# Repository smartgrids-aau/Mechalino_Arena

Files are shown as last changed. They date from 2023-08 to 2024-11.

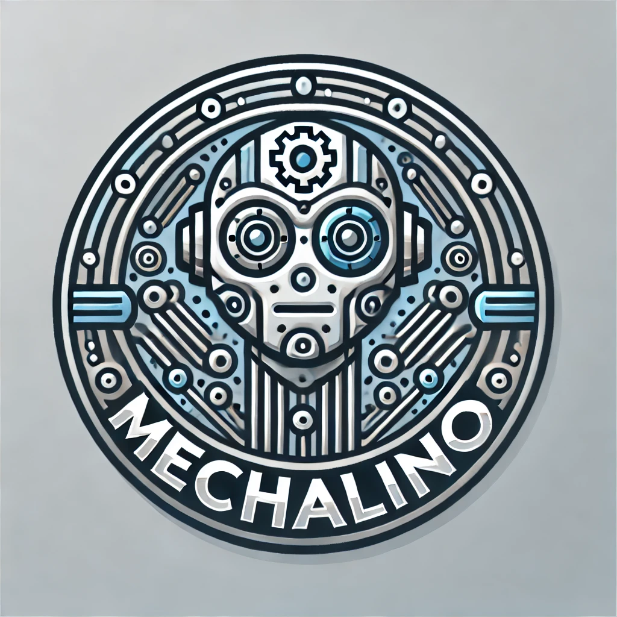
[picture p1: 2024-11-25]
mechalino_robot/hardware/PCB design/layer_2/Redesigned/Images/DALL·E 2024-07-06 23.29.42.webp

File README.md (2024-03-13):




# Mechalino Arena

## Final goal:
Implement the SCPP algorithm to Mechalino robots
## Planned steps::
 - [X] **Step 1.0** - Visualize single layer Mechalino robots in Unity 3D with a ROS backend
 - [ ] **Step 2.0** - Re-implement the SCPP algorithm in ROS
 - [ ] **Step 2.1** - Run the SCPP algorithm in ROS while robots are doing the same movements
 - [ ] **Step 3.0** - Visualize two-layer Mechalino (with sensors) in Unity 3D with a ROS backend
 - [ ] **Step 3.1** - Run the SCPP algorithm in ROS while robots are doing the movements and also delivering sensor data (obstacle detection)
 - [ ] **Step 3.2** - Use two-layer Mechalino robots to run the SCPP algorithm independently and Visualize the result in Unity 3D with a ROS backend
  _____________________________________________________
  
  **[Temporary note]** This is just a raw list and will change. 
_____________________________________________________

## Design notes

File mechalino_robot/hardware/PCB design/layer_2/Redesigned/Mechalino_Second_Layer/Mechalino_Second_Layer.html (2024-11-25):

Reporting Options

# File in Newer Format

Date | : | 30/10/2024
Time | : | 11:04:13
Filename | : | C:\Users\lukak\OneDrive\Dokumente\AAU\Bachelorarbeit\Mechalino_Arena\mechalino_robot\hardware\PCB design\layer_2\Redesigned\Mechalino_Second_Layer\Mechalino_Second_Layer.PrjPcb

Version | Warning

Release 23.10

CAUTION - This project contains rules defined using the Constraint Manager. You are seeing this message for two possible reasons. Firstly, this is an older version of the software that does not support this feature, in which case design rules will fall back to being presented as standard, query-based rules. If you save the PCB project in this older version of Altium Designer, all Constraint Manager data structure information will be lost. Secondly, if this software version does support the feature, then you currently don't have the level of Altium Designer Software Subscription (Pro/Enterprise) to be able to edit constraints using the Constraint Manager, in which case it will present rules in view only mode.

This file was generated by a later version of the software

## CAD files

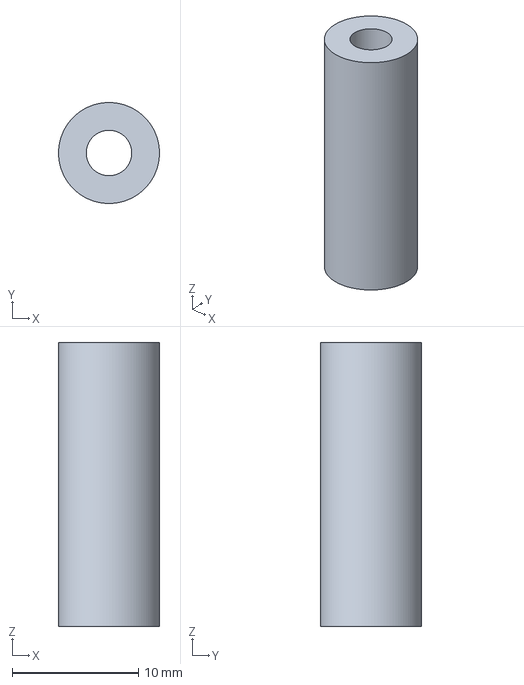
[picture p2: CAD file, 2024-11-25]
mechalino_robot/hardware/3D_designs/layer2.3mf
8.00 x 8.00 x 22.5 mm

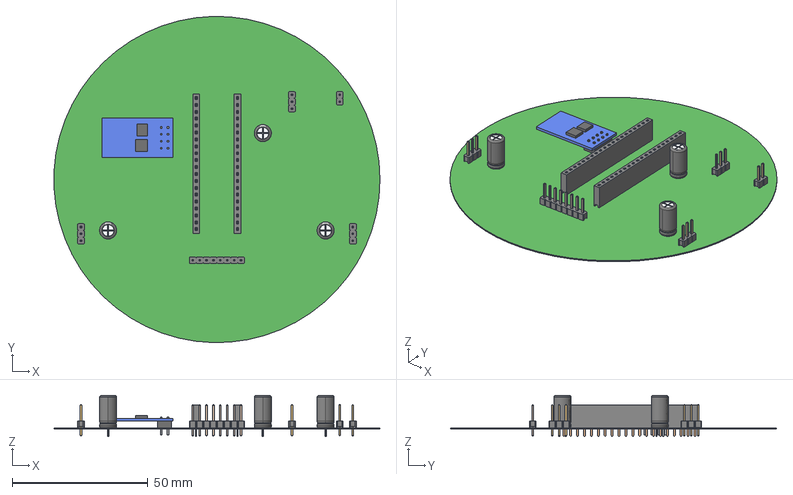
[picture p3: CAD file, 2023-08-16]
mechalino_robot/hardware/PCB design/layer_1/FAB-SwarmlyExplorerBot-A.6/ExportSTEP/PCB.step
119.9 x 120.0 x 15.2 mm
6130xx11121_PIN x 8
6130xx11821_PIN x 40
Extruded x 12
User_Library-Cap-EL(6_3x12-2_5) x 3

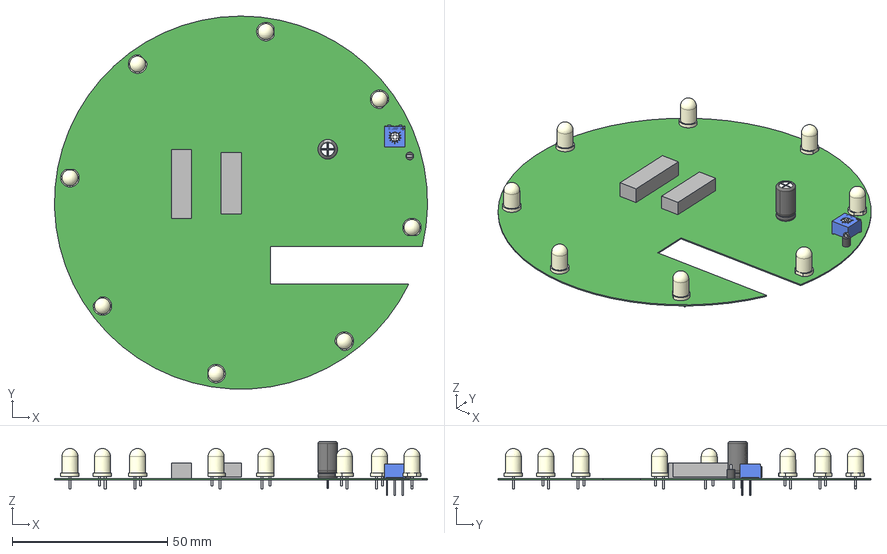
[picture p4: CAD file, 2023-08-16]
mechalino_robot/hardware/PCB design/layer_2/FAB-SwarmlyExplorerBot_layer2-A.8/ExportSTEP/PCB.step
120.0 x 119.9 x 17.5 mm
User_Library-Cap-EL(6_3x12-2_5)
User_Library-Bourns_3362P
Extruded x 2
SNR2-2.54-D5.0MM x 8

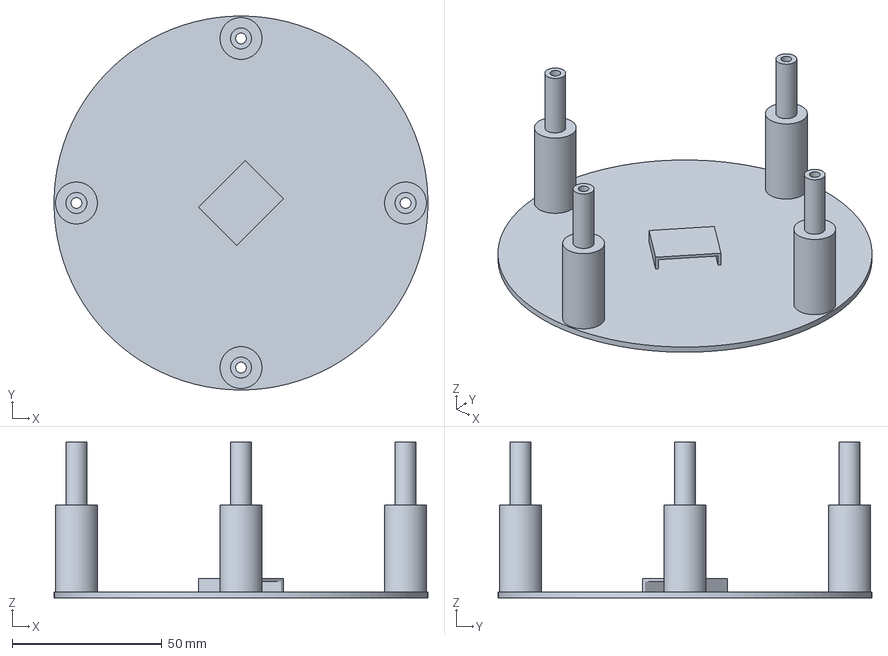
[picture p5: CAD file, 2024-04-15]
mechalino_robot/hardware/3D_designs/Head.3mf
125.0 x 125.0 x 52.0 mm

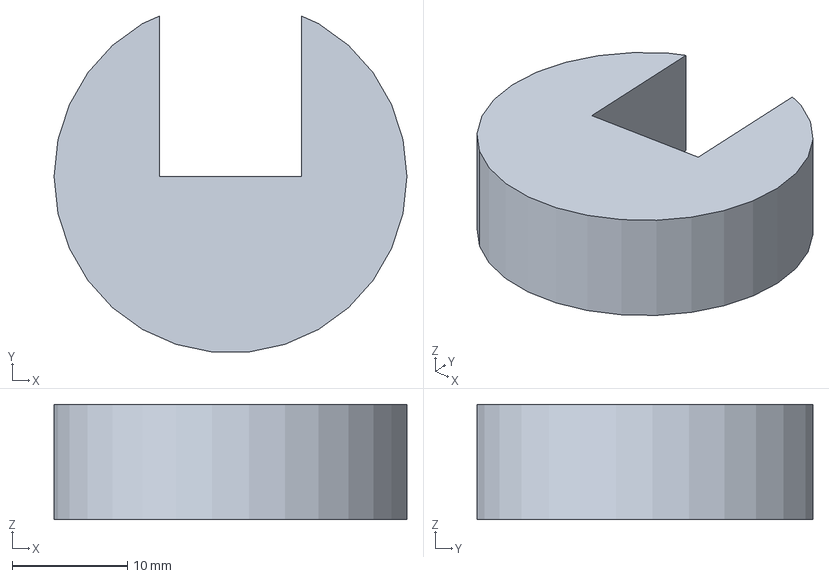
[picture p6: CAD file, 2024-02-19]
mechalino_robot/hardware/3D_designs/obstacle_holder.3mf
30.6 x 29.1 x 10.0 mm

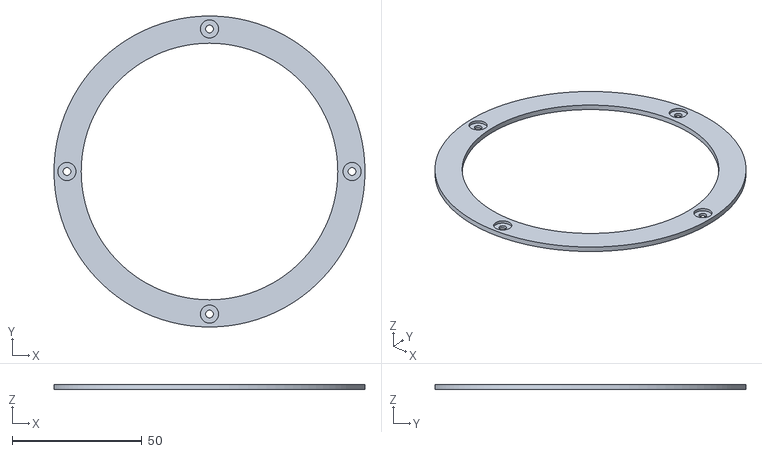
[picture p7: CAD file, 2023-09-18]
mechalino_robot/hardware/3D_designs/Head_p1.stl
120.0 x 120.0 x 2.00

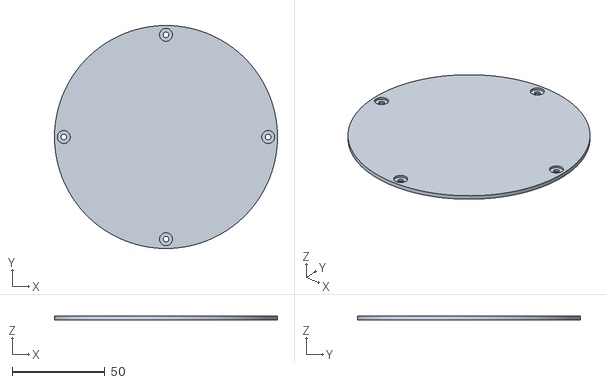
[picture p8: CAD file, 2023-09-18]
mechalino_robot/hardware/3D_designs/Head_p2.stl
120.0 x 120.0 x 2.00

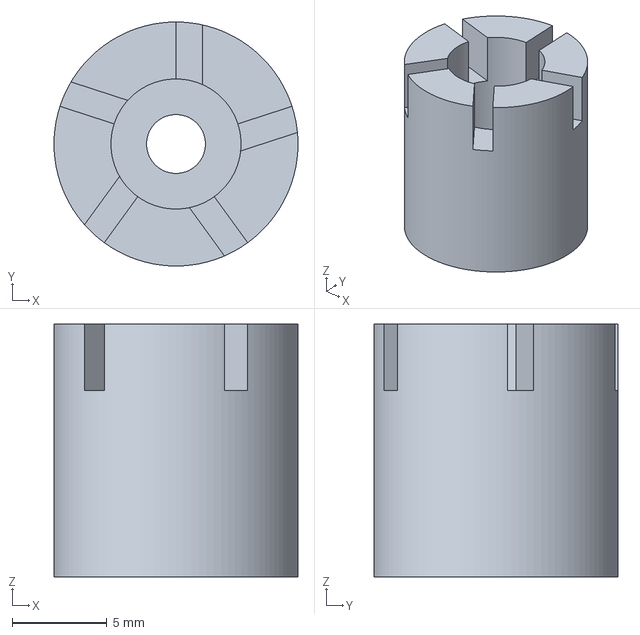
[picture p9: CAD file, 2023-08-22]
mechalino_robot/hardware/3D_designs/wheels1.3mf
12.8 x 12.8 x 13.3 mm

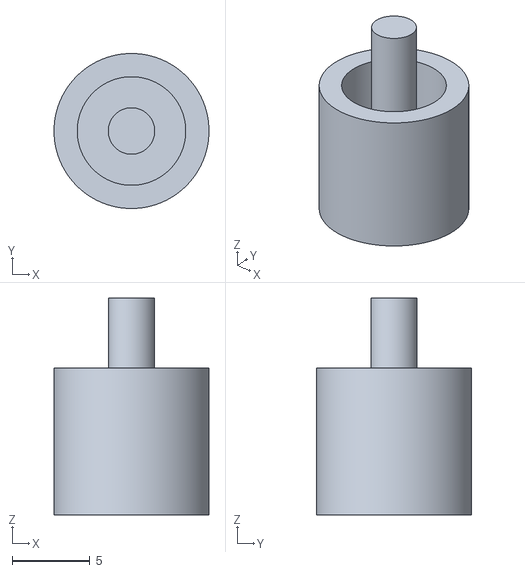
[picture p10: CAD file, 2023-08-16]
mechalino_robot/hardware/3D_designs/wheels5.stl
10.0 x 10.0 x 14.0

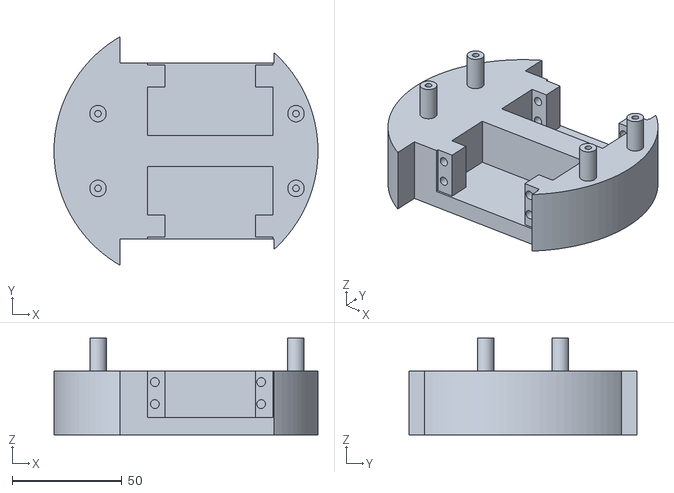
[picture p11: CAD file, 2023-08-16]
mechalino_robot/hardware/3D_designs/body.stl
120.0 x 103.9 x 44.0

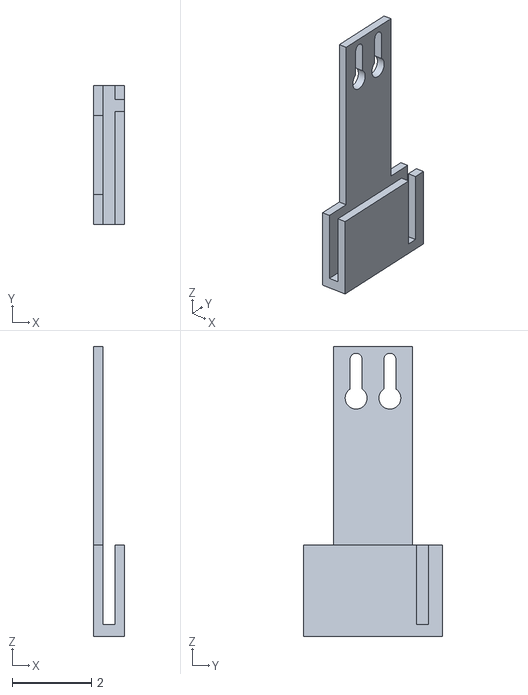
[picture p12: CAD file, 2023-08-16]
mechalino_robot/hardware/3D_designs/camera_holder.stl
0.79 x 3.50 x 7.30

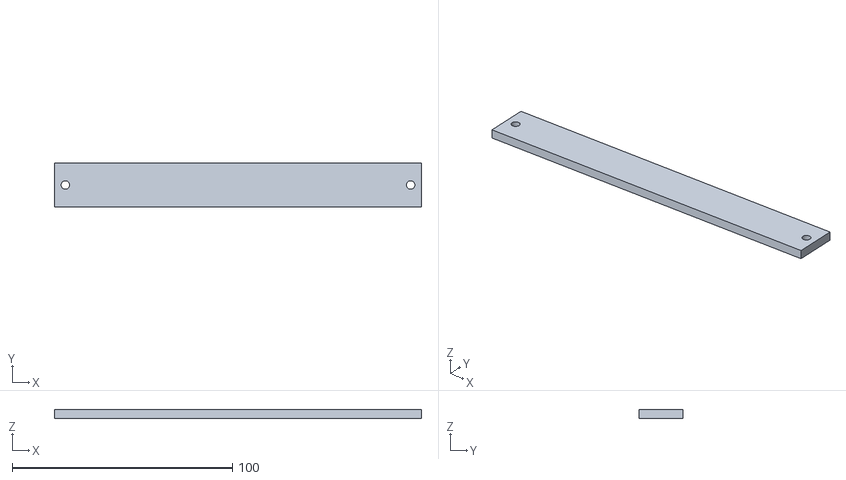
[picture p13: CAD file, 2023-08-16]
mechalino_robot/hardware/3D_designs/camera_holder_V2_Top.stl
166.7 x 20.0 x 4.00

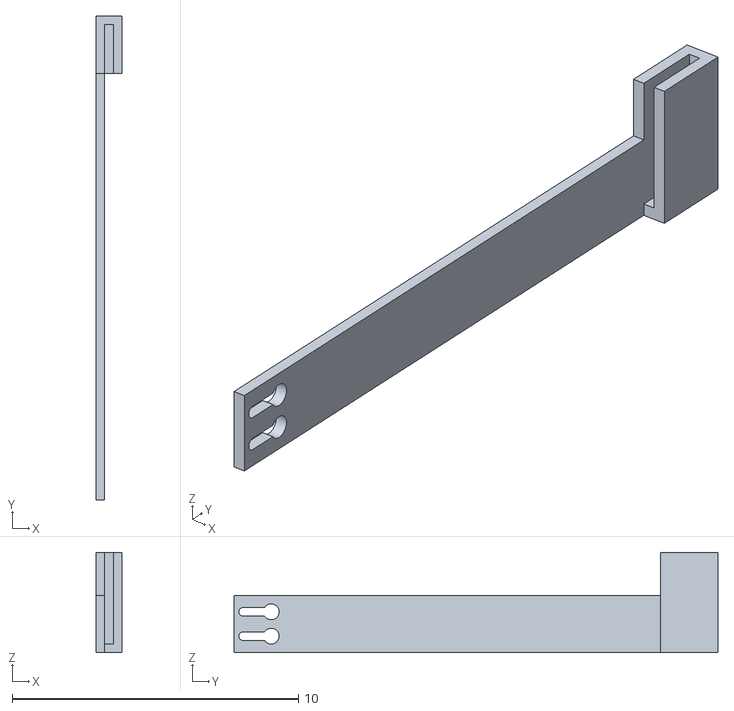
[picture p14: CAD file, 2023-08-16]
mechalino_robot/hardware/3D_designs/camera_holder_bottom.stl
0.9 x 16.9 x 3.50

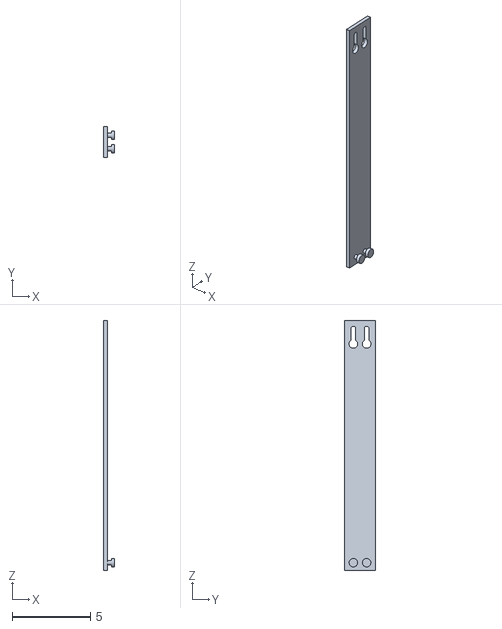
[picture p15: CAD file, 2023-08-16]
mechalino_robot/hardware/3D_designs/camera_holder_extention.stl
0.72 x 2.00 x 16.0

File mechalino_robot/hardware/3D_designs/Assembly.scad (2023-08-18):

use <main1.scad>
use <servo.scad>
use <wheels1.scad>
use <Head.scad>

color("MediumBlue")main();

translate([-10,10.1,0]) color("red") servo();
mirror([0,1,0])translate([-9,10.1,0]) color("red") servo();
translate([0,55,10])rotate([-90,0,0])color("Gray")wheels();
mirror([0,1,0])translate([0,55,10])rotate([-90,0,0])color("Gray")wheels();
translate([0,0,35])head();

translate([0,60,10])rotate([-90,0,0])cylinder(19,47/2,47/2);
mirror([0,1,0])translate([0,60,10])rotate([-90,0,0])cylinder(19,47/2,47/2);

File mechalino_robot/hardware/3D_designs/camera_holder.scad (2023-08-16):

$fn = 100;
/*
union()
{
    translate([0.8,-2,2.3])
    {
        rotate([0,-180,0])
        {
            difference()
            {
                translate([0,2,0])
                {
                    cube([0.79,3.5,3.3]);
                }
                translate([-2.1,-0.1,2.3])
                {
                    cube([4.7,7,2.3]);
                };
                translate([0.25,-0.1,-0.3])
                {
                    cube([0.3,7,2.3]);
                };
                translate([-0.1,4.84,-0.3])
                {
                    cube([0.5,0.305,2.3]);
                };
                translate([-0.1,-0.1,-0.3])
                {
                    cube([0.5,0.65,2.3]);
                };
                translate([-0.1,6.25,-0.3])
                {
                    cube([0.5,1,2.3]);
                };
            }
        }
    }
    
    translate([0,0.75,0])
    {
        difference()
        {
            translate([0.01,0,2.2])
                cube([0.24,2,5.1]);
            translate([0.4,0.575,6])
            {
                rotate([0,-90,0])
                {
                    union()
                    {
                        cylinder(0.5,0.275,0.275);
                        translate([0,-0.15,0])
                            cube([1,0.3,0.5]);
                        
                        translate([0.98,0,0])
                            cylinder(0.5,0.15,0.15);
                    }
                }
            }
            
            translate([0.4,1.425,6])
            {
                rotate([0,-90,0])
                {
                    union()
                    {
                        cylinder(0.5,0.275,0.275);
                        translate([0,-0.15,0])
                            cube([1,0.3,0.5]);
                        
                        translate([0.98,0,0])
                            cylinder(0.5,0.15,0.15);
                    }
                }
            }
        }
    }
}
*/
translate([-0.23,0.8,10])
    {
        difference()
        {
            translate([0.01,0,-3.5])
                cube([0.24,2,16]);
            translate([0.4,0.575,11])
            {
                rotate([0,-90,0])
                {
                    union()
                    {
                        cylinder(0.5,0.275,0.275);
                        translate([0,-0.15,0])
                            cube([1,0.3,0.5]);
                        
                        translate([0.98,0,0])
                            cylinder(0.5,0.15,0.15);
                    }
                }
            }
            
            translate([0.4,1.425,11])
            {
                rotate([0,-90,0])
                {
                    union()
                    {
                        cylinder(0.5,0.275,0.275);
                        translate([0,-0.15,0])
                            cube([1,0.3,0.5]);
                        
                        translate([0.98,0,0])
                            cylinder(0.5,0.15,0.15);
                    }
                }
            }
        }
        translate([0,1.425,-3])
        {
            rotate([0,90,0])cylinder(0.23+0.23+0.1,0.14,0.14);
            translate([0.23+0.23+0.05,0,0])rotate([0,90,0])cylinder(0.2,0.270,0.270);
        }
        translate([0.01,0.575,-3])
        {
            rotate([0,90,0])cylinder(0.23+0.23+0.1,0.14,0.14);
            translate([0.23+0.23+0.05,0,0])rotate([0,90,0])cylinder(0.2,0.270,0.270);
        }
    }
/*rotate([0,90,0])
{
    translate([0,0,0])
    {
        union()
        {
            cylinder(0.5,0.275,0.275);
            translate([0,-0.15,0])
                cube([1,0.3,0.5]);
        }
    }
}*/

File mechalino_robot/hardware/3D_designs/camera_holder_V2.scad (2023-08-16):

$fn = 100;
/*difference()
{
    cube([151+3+3.85+1+1+3.85+3,20,4]);

    translate([151+3+3.85+1+1+3.85/2,10,-1])
    {
        cylinder(h=6,d=3.85);
    }
    
    translate([3+3.85/2,10,-1])
    {
        cylinder(h=6,d=3.85);
    }
}*/
/*translate([3+3.85+1,10,2])
    cube([151,20,4]);*/
err = 0.2;
hs = 4.1+err;    
thk = 3;
union(){
    difference()
    {
        union()
        {
            translate([(151+3+hs+1+1+hs+3)/2+(41+thk*2+err)/2,10+(59+thk*2+err)/2,0])
            {
                rotate([0,0,90])
                {
                    rotate([0,0,90])
                    {
                        difference()
                        {
                            cube([151+3+hs+1+1+hs+3,20,4]);

                            translate([151+3+hs+1+1+hs/2,10,-1])
                            {
                                cylinder(h=6,d=hs);
                            }
                            
                            translate([3+hs/2,10,-1])
                            {
                                cylinder(h=6,d=hs);
                            }
                        }
                    }
                }
            }
            cube([41+thk*2+err,59+thk*2+err,25+thk+err]);
        }
        translate([thk,thk,thk])
            cube([41+err,59+err,25+thk+err+1]);
        translate([5.5,-1,thk+8])
            cube([41-5.5*2+thk*2+err,59+2+thk*2+err,25+thk*2+err]);
        translate([-1,5.5,thk+8])
            cube([41+2+thk*2+err,59-5.5*2+thk*2+err,25+thk*2+err]);
        translate([thk+3,thk+3,-1])
            cube([41-6+err,59-6,thk+2]);
    };
};    


        

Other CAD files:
mechalino_robot/hardware/3D_designs/camera_holder_mid_S_S.stl
mechalino_robot/hardware/3D_designs/camera_holder_V2_Bottom.3mf
mechalino_robot/hardware/3D_designs/head2.stl
mechalino_robot/hardware/3D_designs/Head.scad
mechalino_robot/hardware/3D_designs/Head.stl
mechalino_robot/hardware/3D_designs/camera_holder_V2_Bottom.stl
mechalino_robot/hardware/3D_designs/layer2.scad
mechalino_robot/hardware/3D_designs/layer2.stl
mechalino_robot/hardware/3D_designs/main1.scad
mechalino_robot/hardware/3D_designs/obstacle_holder.scad
mechalino_robot/hardware/3D_designs/obstacle_holder.stl
mechalino_robot/hardware/3D_designs/servo.scad
mechalino_robot/hardware/3D_designs/wheels1.scad
mechalino_robot/hardware/3D_designs/wheels1.stl

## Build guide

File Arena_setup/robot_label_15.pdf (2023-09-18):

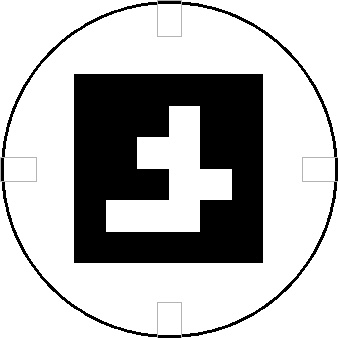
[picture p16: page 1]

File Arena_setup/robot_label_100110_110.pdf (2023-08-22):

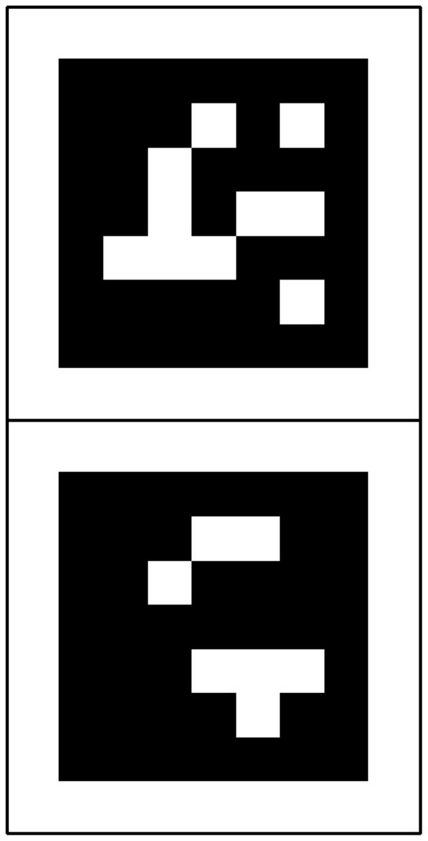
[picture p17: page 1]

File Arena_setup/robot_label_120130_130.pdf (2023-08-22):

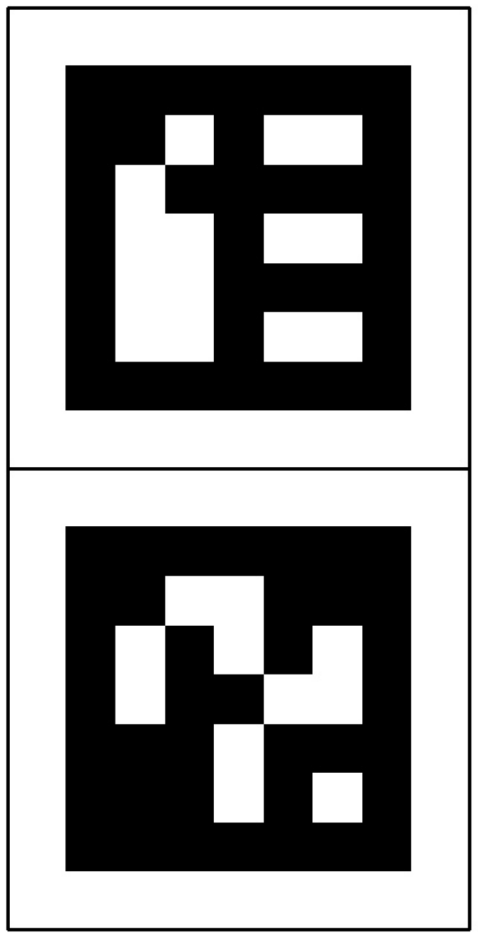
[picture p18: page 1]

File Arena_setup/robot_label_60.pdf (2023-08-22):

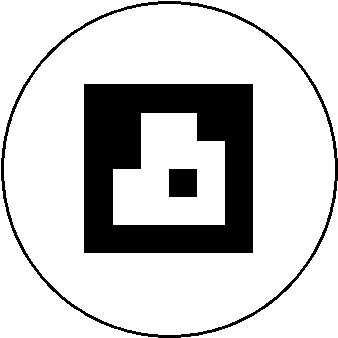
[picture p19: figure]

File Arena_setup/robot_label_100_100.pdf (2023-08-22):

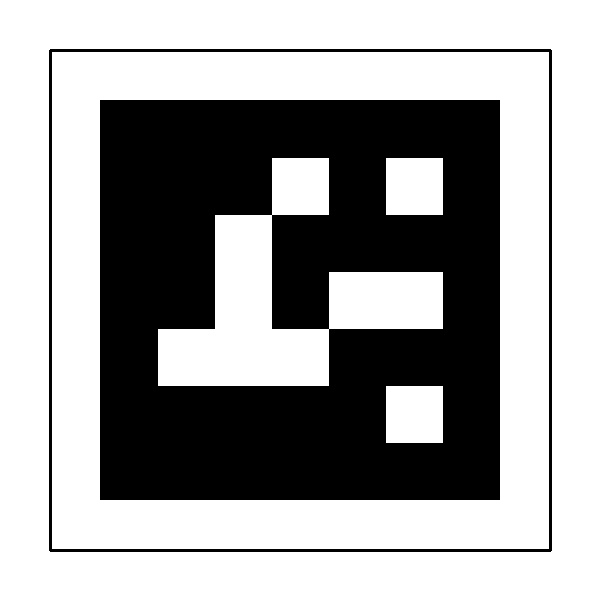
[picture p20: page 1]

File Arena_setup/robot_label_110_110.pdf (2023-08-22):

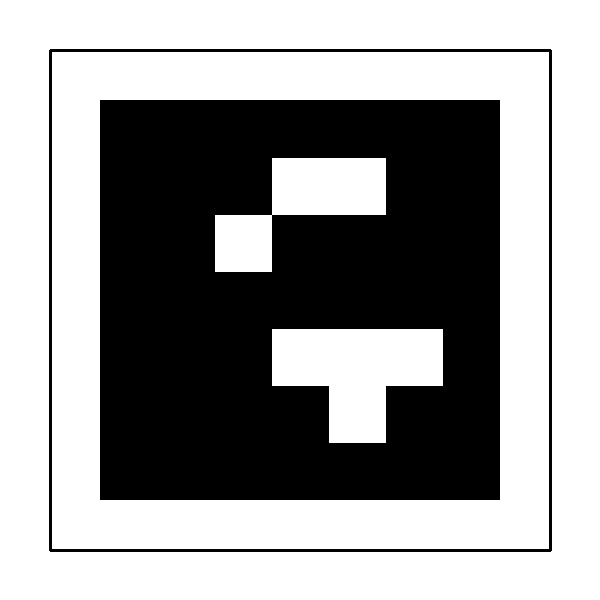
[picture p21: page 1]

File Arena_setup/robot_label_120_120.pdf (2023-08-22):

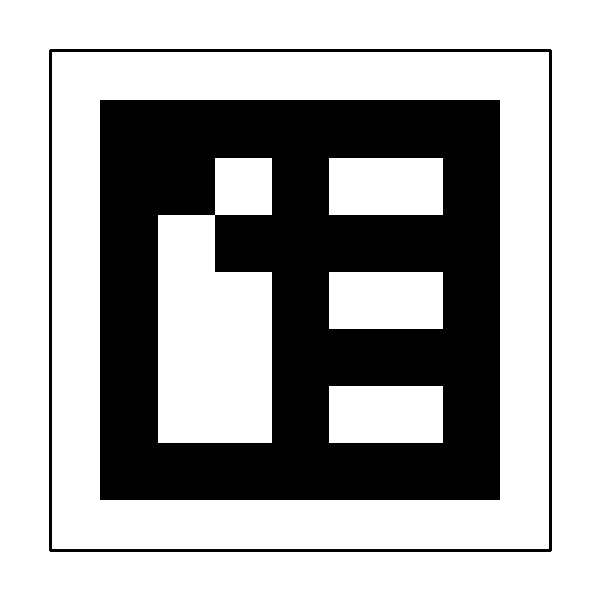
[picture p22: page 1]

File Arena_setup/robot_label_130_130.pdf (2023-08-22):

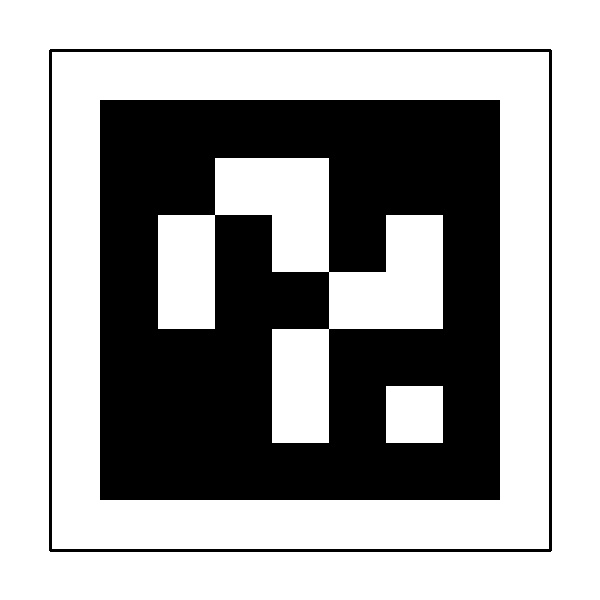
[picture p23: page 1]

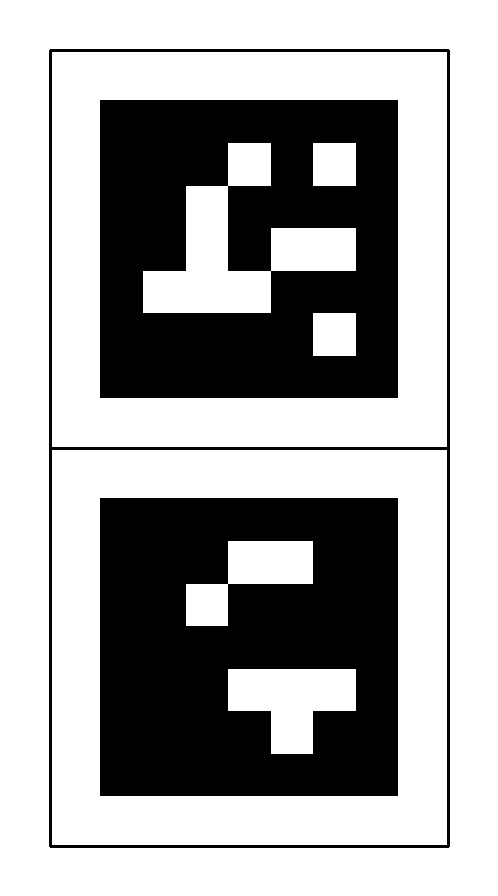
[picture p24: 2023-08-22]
Arena_setup/robot_label_100110.jpg

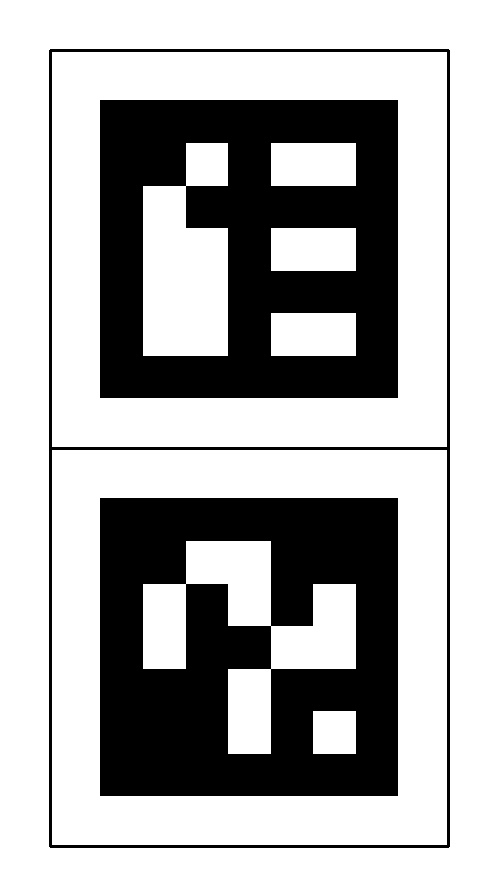
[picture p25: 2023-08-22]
Arena_setup/robot_label_120130.jpg

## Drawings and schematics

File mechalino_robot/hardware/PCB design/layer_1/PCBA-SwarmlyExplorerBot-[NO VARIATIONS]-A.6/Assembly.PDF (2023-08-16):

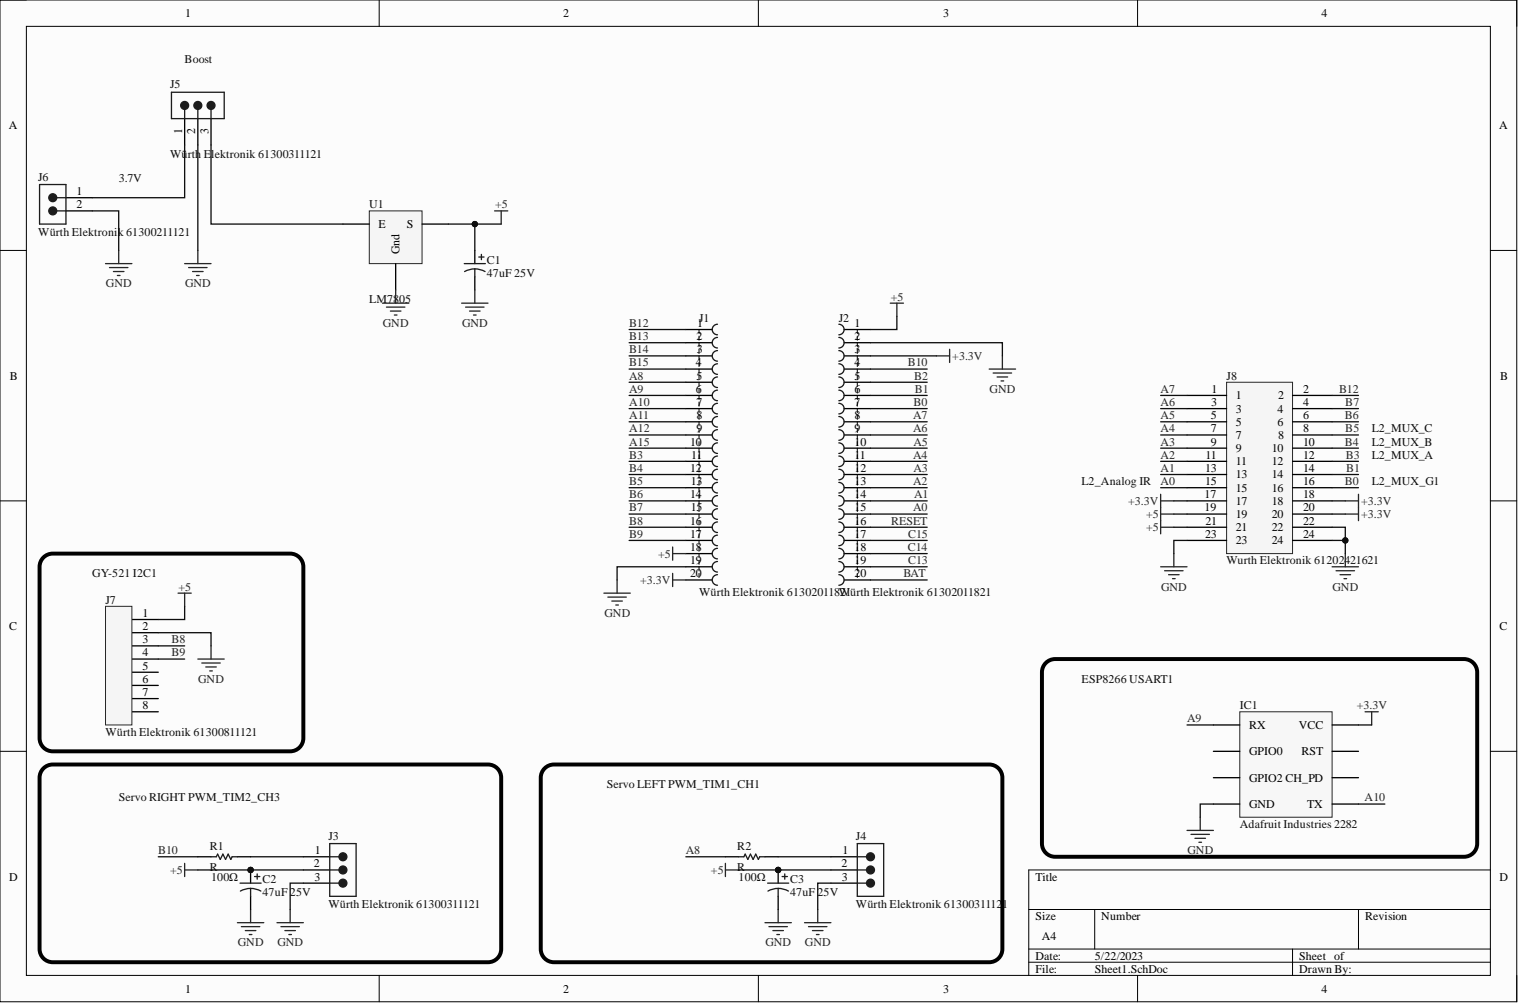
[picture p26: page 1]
EFT PWM_; o RIG; T PWM_; +5 GND; IC1 Adafru

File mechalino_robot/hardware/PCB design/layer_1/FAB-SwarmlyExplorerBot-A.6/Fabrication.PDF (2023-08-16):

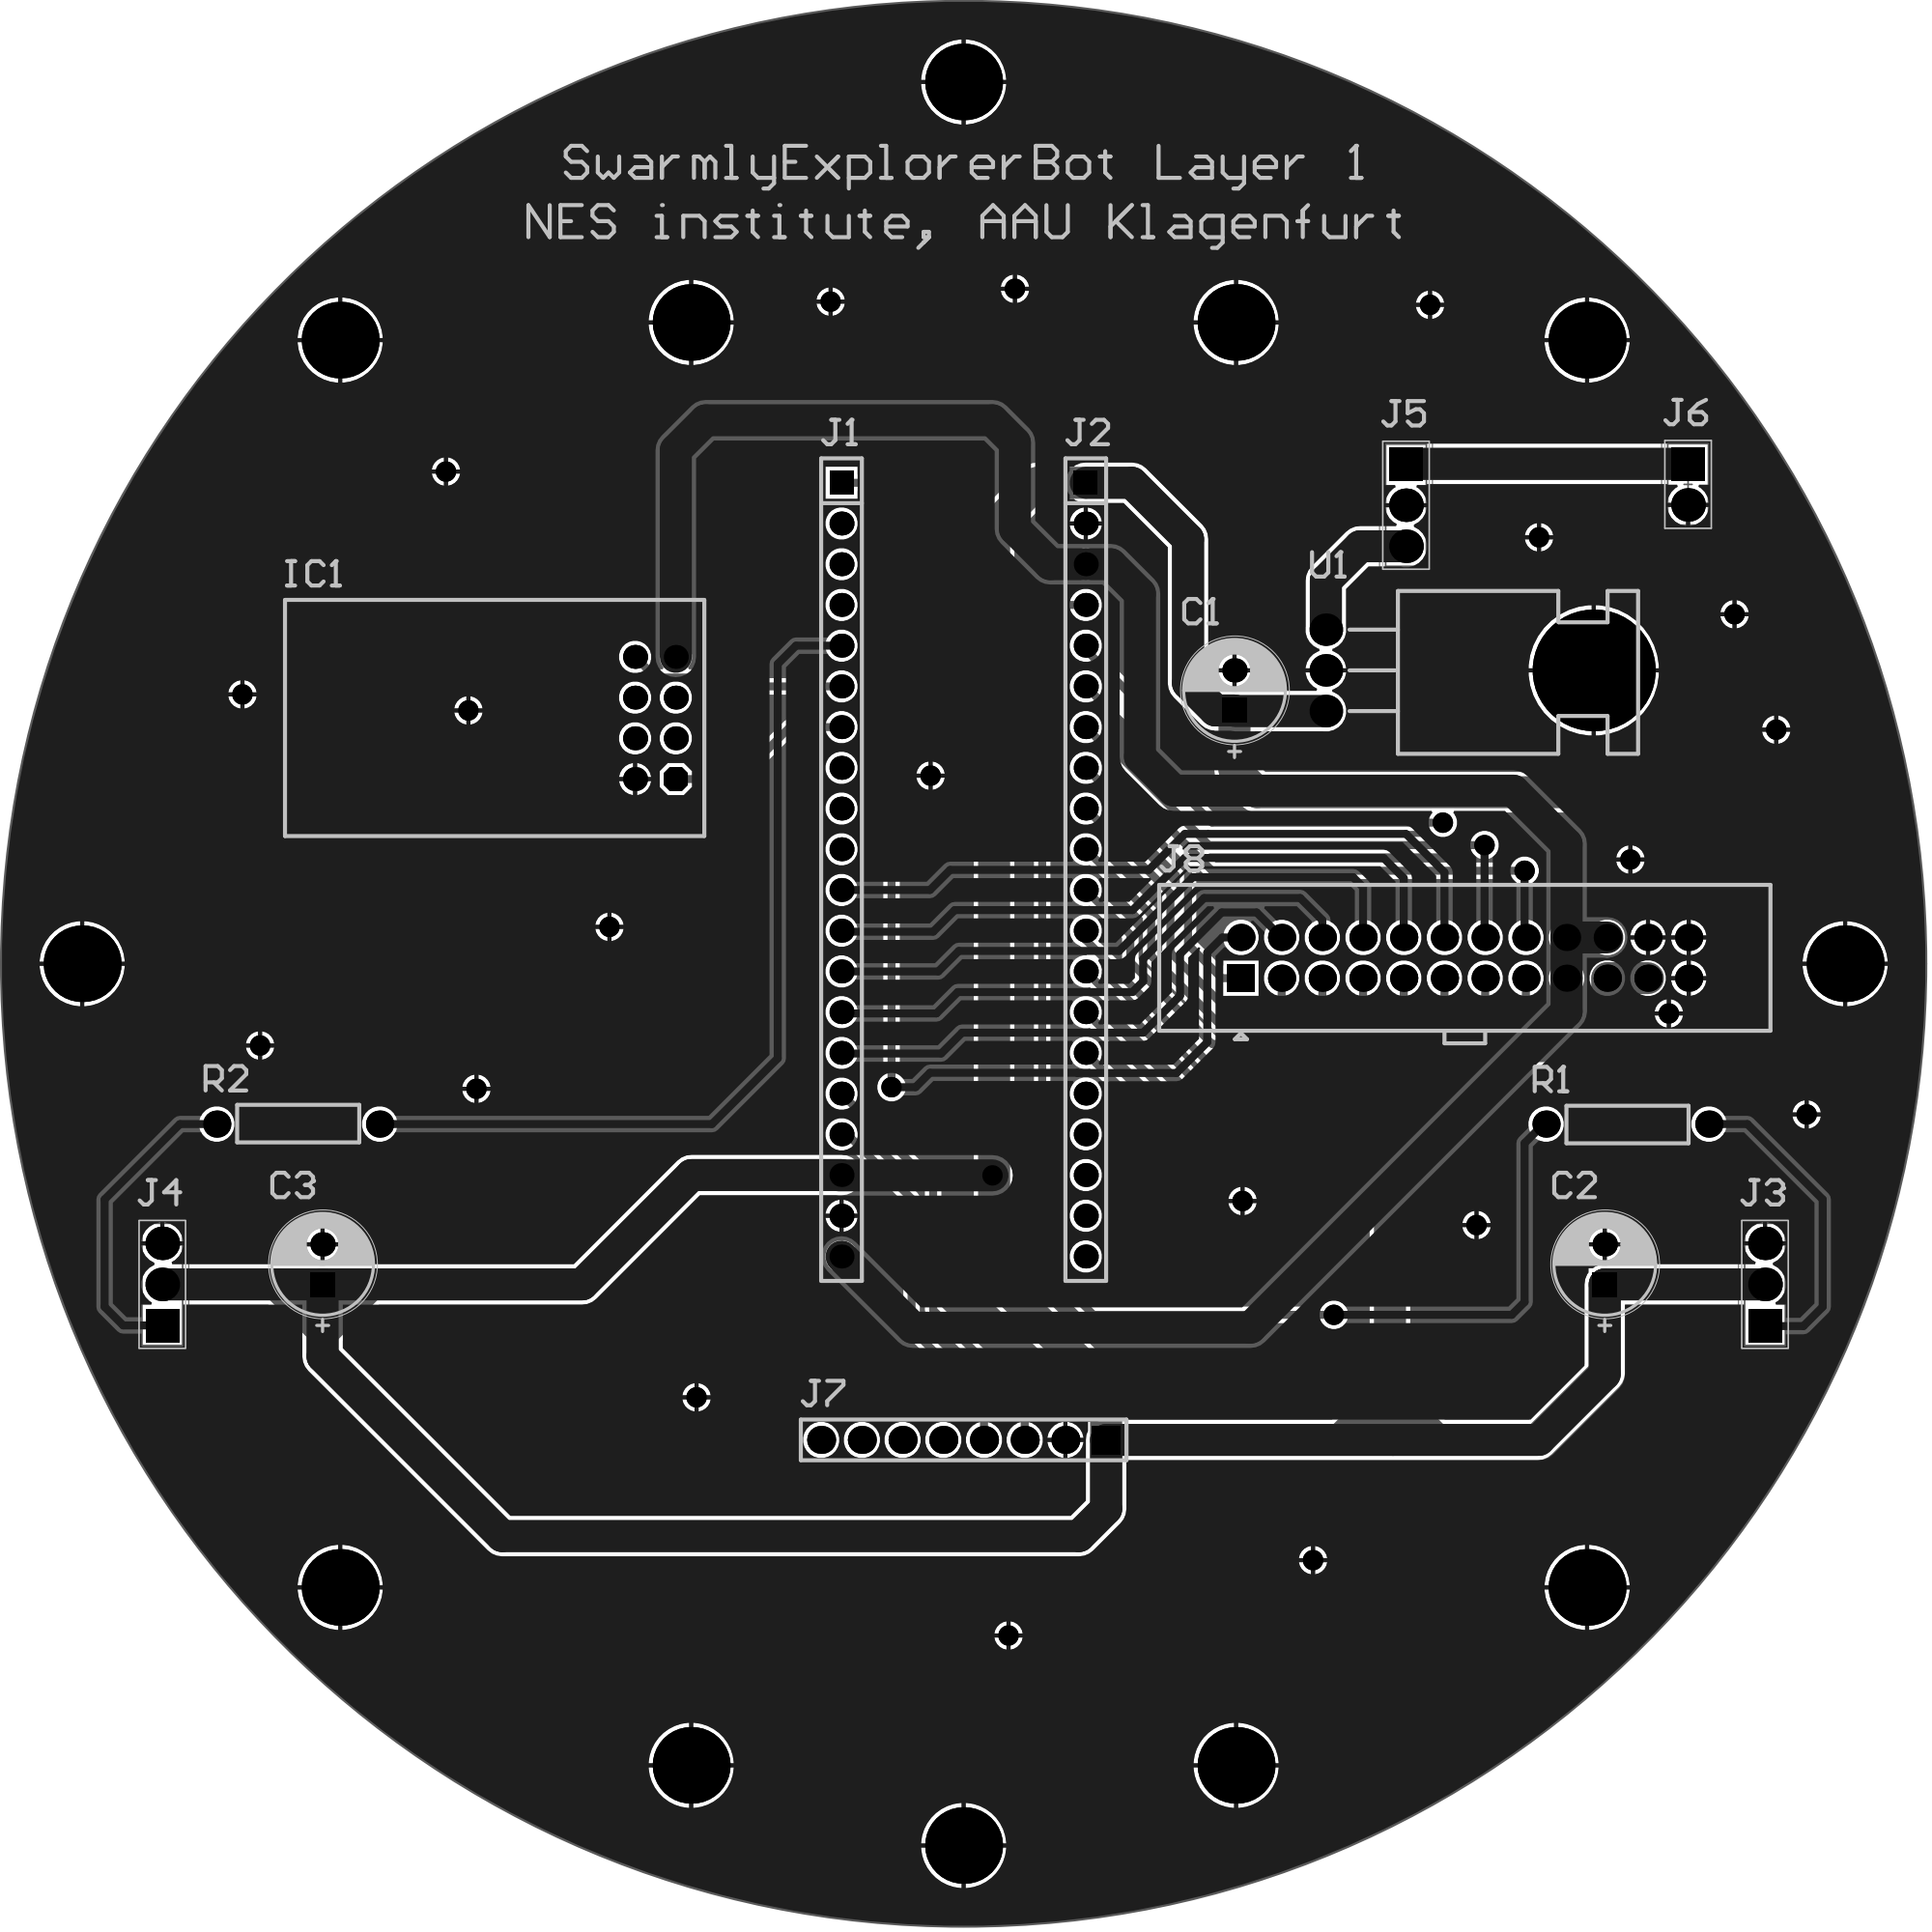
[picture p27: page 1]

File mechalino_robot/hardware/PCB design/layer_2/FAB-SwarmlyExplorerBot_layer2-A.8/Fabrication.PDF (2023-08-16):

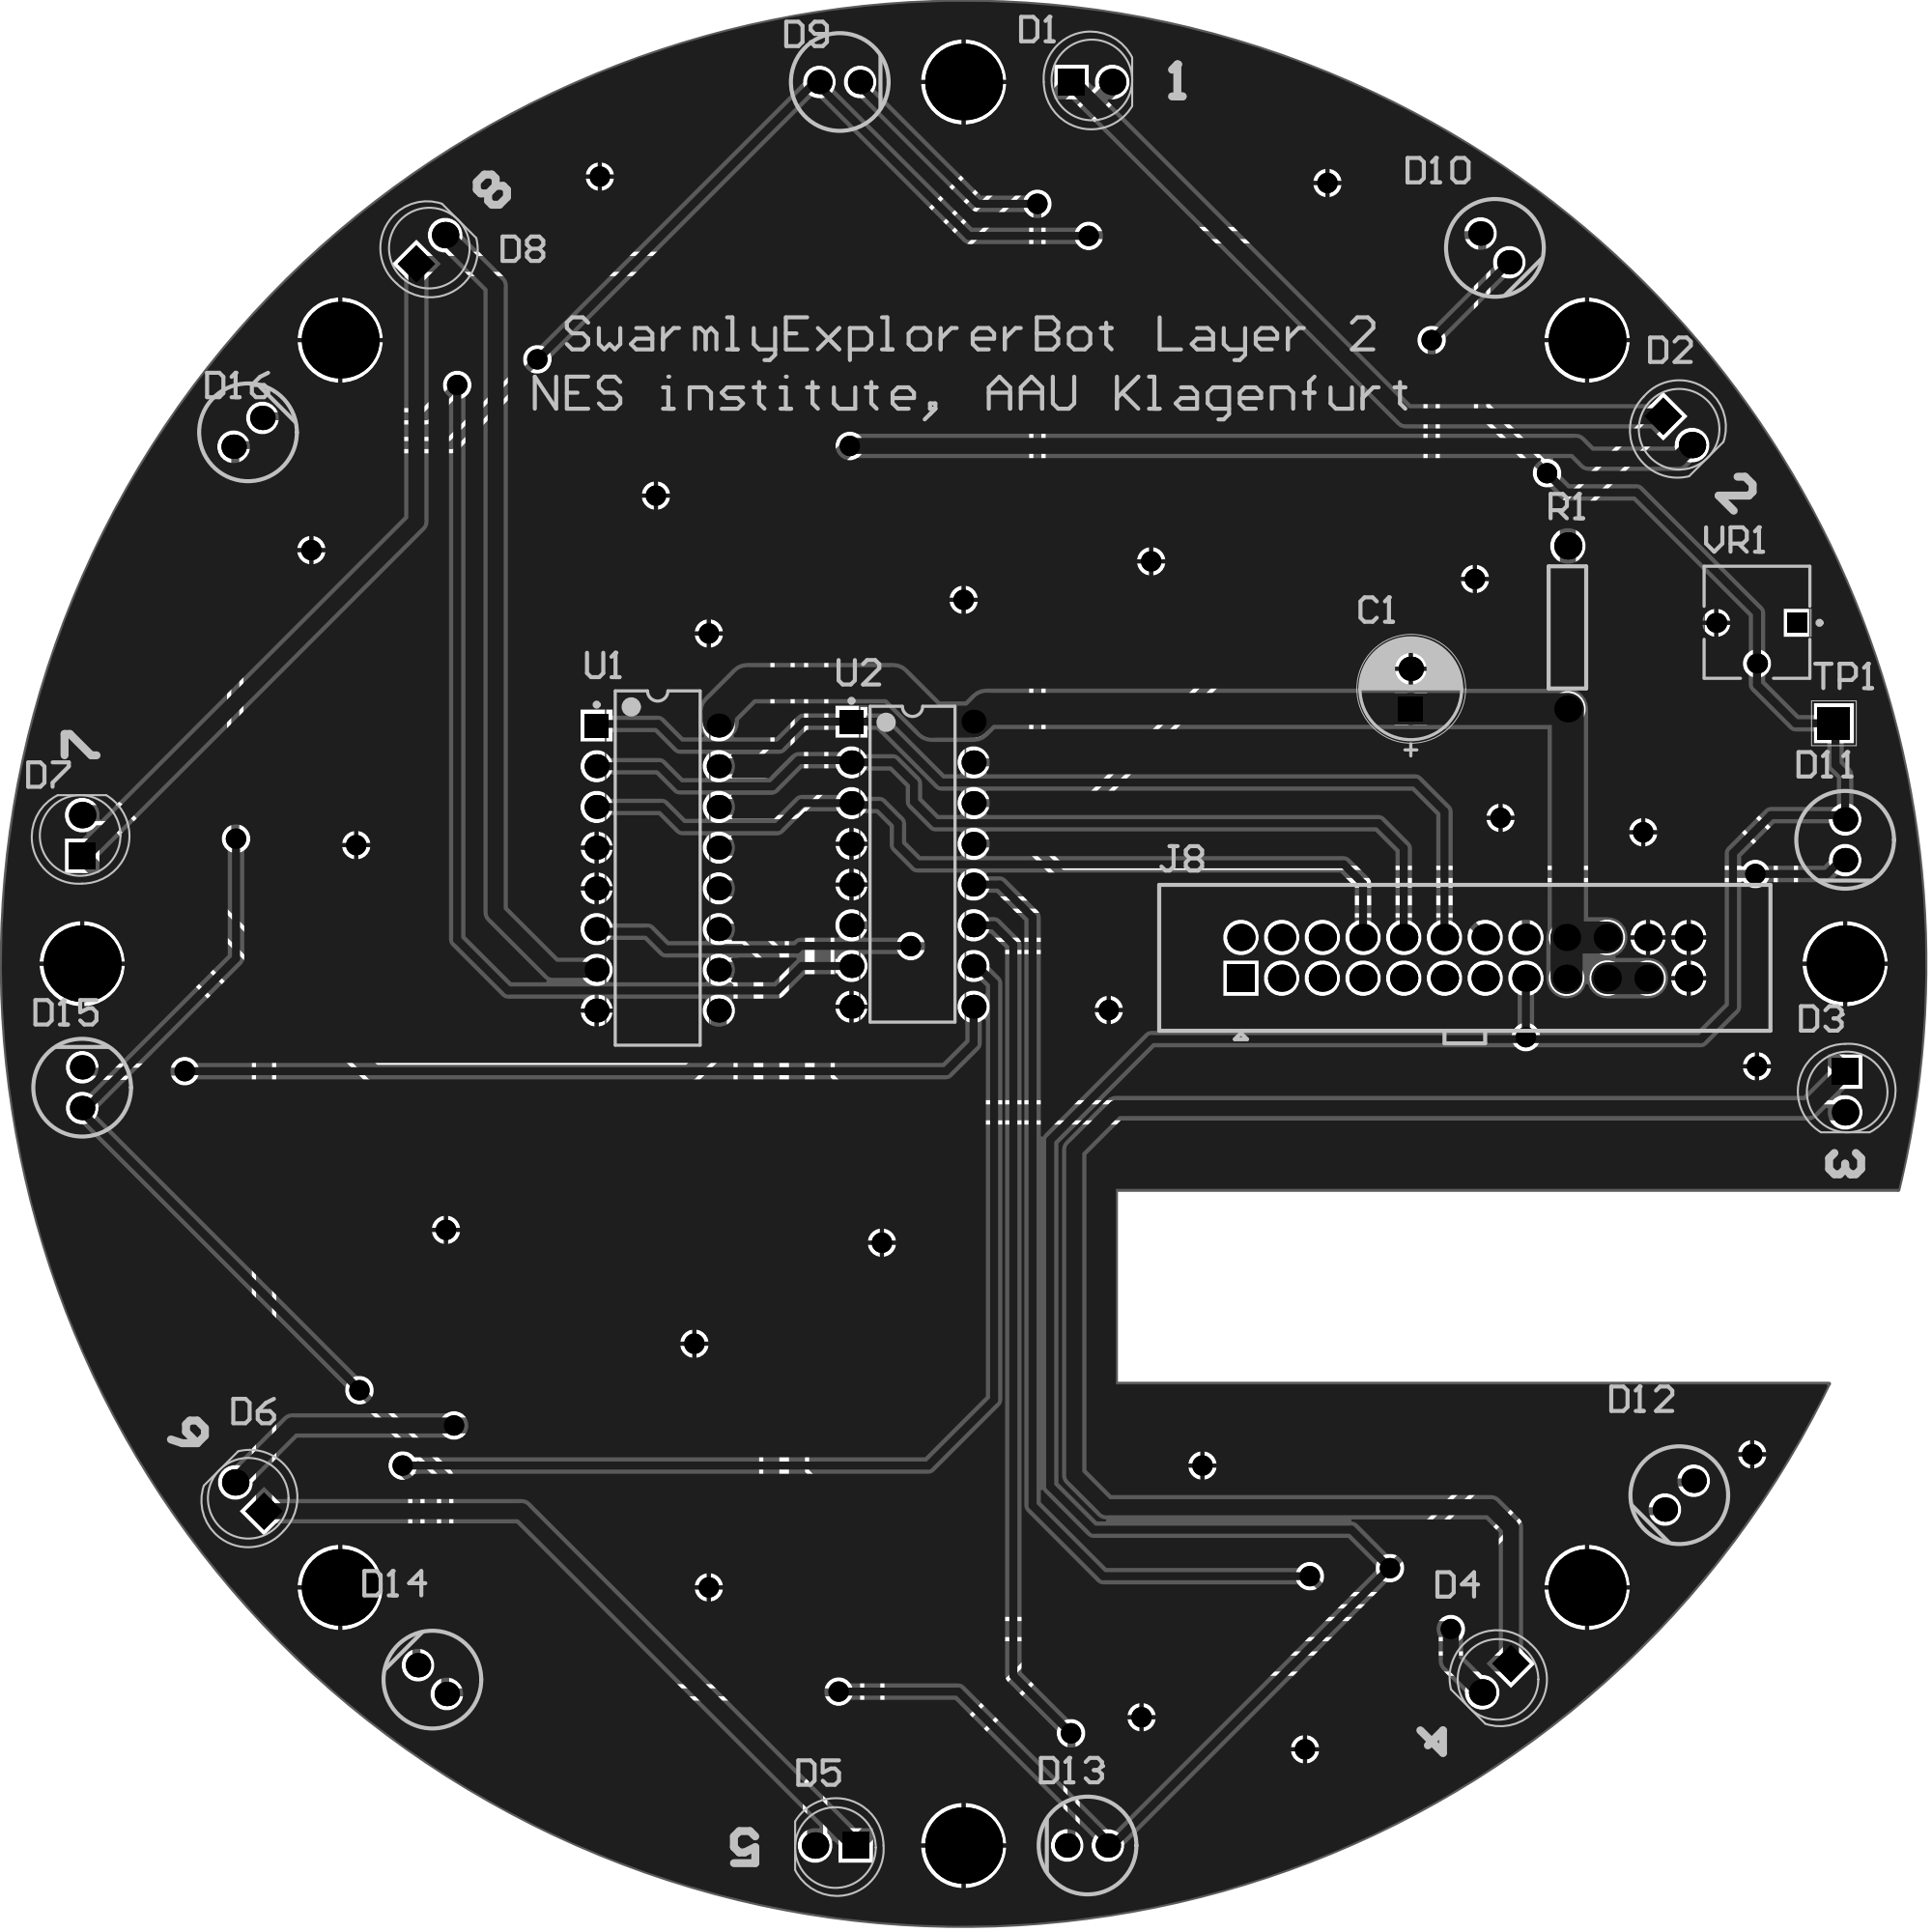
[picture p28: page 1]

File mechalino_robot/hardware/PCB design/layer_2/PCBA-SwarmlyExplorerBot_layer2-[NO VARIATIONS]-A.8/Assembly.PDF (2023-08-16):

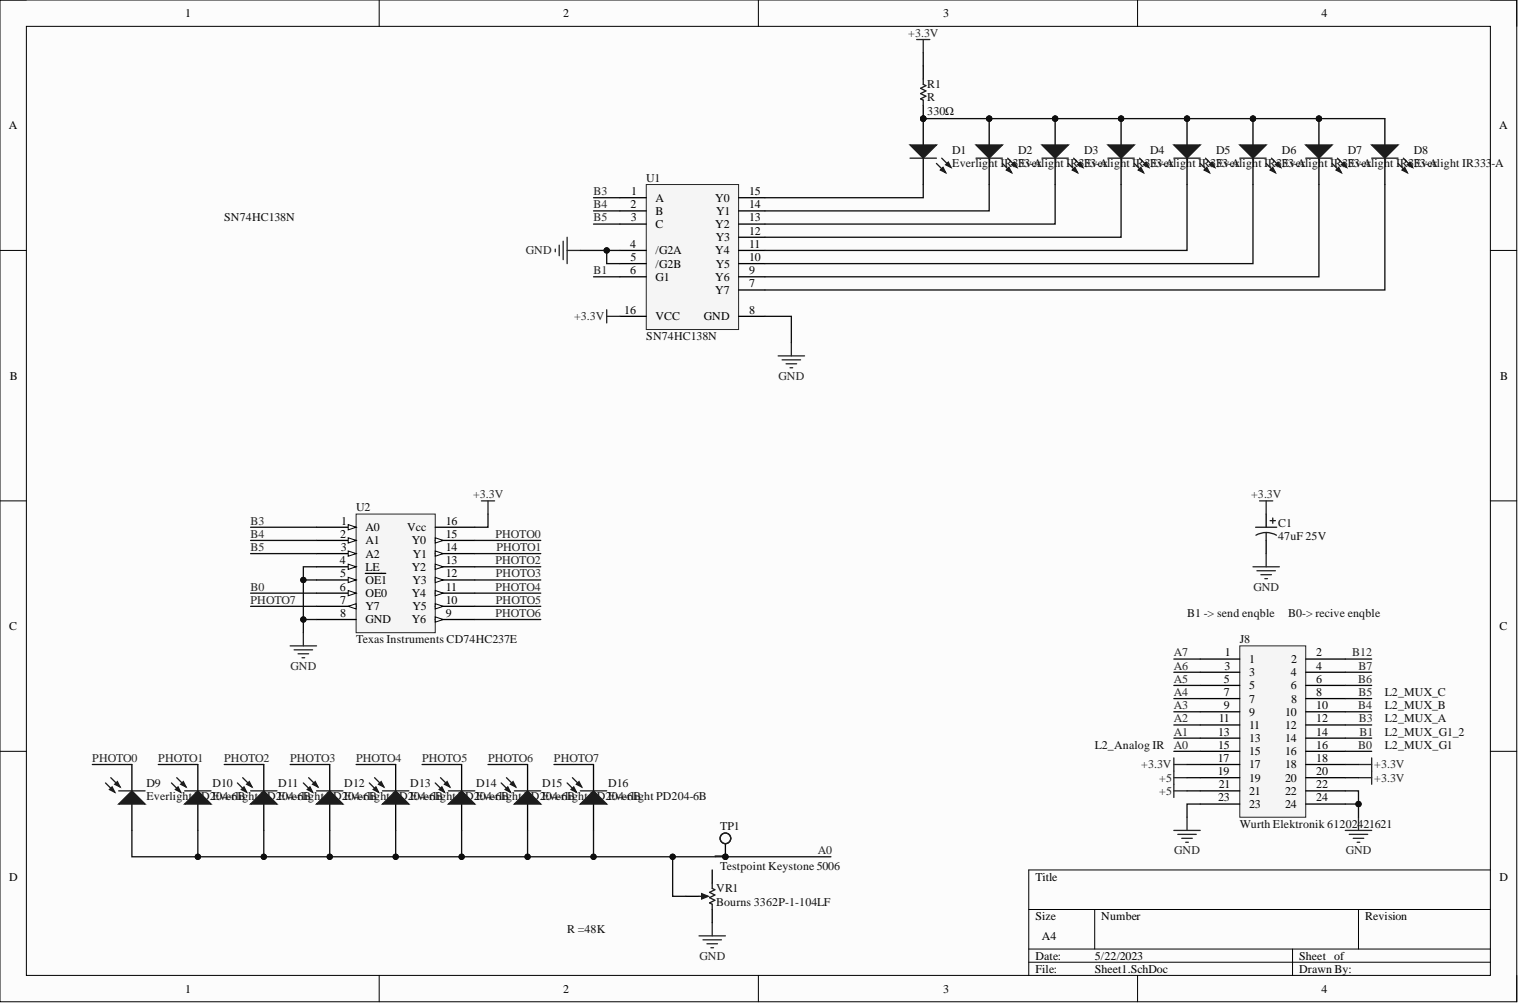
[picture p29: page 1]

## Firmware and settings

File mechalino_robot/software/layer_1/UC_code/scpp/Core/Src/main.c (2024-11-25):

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
/* Includes ----------------------------------------------*/
#include "main.h"
#include "adc.h"
#include "i2c.h"
#include "tim.h"
#include "usart.h"
#include "gpio.h"

/* USER CODE BEGIN Includes */
#include <string.h>
#include <stdlib.h>
#include <stdio.h>
#include <math.h>
#include <inttypes.h>  // Include for uint16_t format specifiers
/* USER CODE END Includes */

/* USER CODE BEGIN PTD */
typedef struct {
	TIM_HandleTypeDef *htim;
	uint32_t channel;
	uint32_t current_pwm;
} Servo;

typedef enum {
	IDLE, ROTATING, MOVING, SPINNING
} RobotState;

typedef struct {
	float integral;
	float previous_error;
	float kp;
	float ki;
	float kd;
	float integral_limit;
	float output_limit;
} PIDController;

/* USER CODE END PTD */

/* USER CODE BEGIN PD */

/* PWM Values for Servo Control */
#define BACKWARD_MAX 800 	// Maximum backward speed
#define BACKWARD_SLOW 2800 	// Minimum backward speed
#define SERVO_STOP 3000
#define FORWARD_MAX 5100 	// Maximum forward speed
#define FORWARD_SLOW 3250 	// Minimum forward speed
/* Base Speeds for Each Motor */
#define BASE_SPEED_FORWARD 4175    // Base PWM for forward speed
#define BASE_SPEED_BACKWARD 1800   // Base PWM for backward speed
/* Maximum Correction Value */
#define MAX_CORRECTION 900      // Maximum correction value for pid

/* Thresholds and PID Gains */
#define ANGLE_THRESHOLD_ROTATE_TO_MOVE  3.0f  	// Degrees
#define ANGLE_THRESHOLD_MOVE_TO_ROTATE 30.0f  	// Degrees
#define DISTANCE_THRESHOLD_MOVE_TO_STOP 0.12f  	// Stop moving when within this distance
#define DISTANCE_THRESHOLD_STOP_TO_MOVE 0.15f	// Start moving again when beyond this distance

#define KP_ROTATION 10.0f 	// Proportional gain for rotation
#define KI_ROTATION 0.0f 	// Integral gain for rotation
#define KD_ROTATION 3.0f 	// Derivative gain for rotation

/* Maximum Integral Term */
#define MAX_INTEGRAL 1000.0f   // Limit for integral term

#define KP_MOVEMENT 15.0f	// Proportional gain for movement
#define KI_MOVEMENT 0.2f	// Integral gain for movement
#define KD_MOVEMENT 3.0f	// Derivative gain for movement

#define MAX_COORDS 100		// Maximum number of coordinates in path

#define SERIAL_SEND_INTERVAL 1000	// Interval in ms to send data over serial
/* USER CODE END PD */


/* USER CODE BEGIN PV */
Servo servo_left = { &htim1, TIM_CHANNEL_1, SERVO_STOP };
Servo servo_right = { &htim2, TIM_CHANNEL_3, SERVO_STOP };

volatile RobotState current_state = IDLE;

PIDController rotation_pid = { .integral = 0.0f, .previous_error = 0.0f, .kp =
KP_ROTATION, .ki = KI_ROTATION, .kd = KD_ROTATION, .integral_limit =
MAX_INTEGRAL, .output_limit = MAX_CORRECTION }; // Tuning for rotation
PIDController movement_pid = { .integral = 0.0f, .previous_error = 0.0f, .kp =
KP_MOVEMENT, .ki = KI_MOVEMENT, .kd = KD_MOVEMENT, .integral_limit =
MAX_INTEGRAL, .output_limit = MAX_CORRECTION }; // Tuning for movement

char rx_buffer[256];
uint8_t rx_index = 0;
volatile int rx_complete = 0;
uint8_t UART1_rxBuffer[1] = { 0 };

float current_x = 0.0f;
float current_y = 0.0f;
float current_yaw = 0.0f;

float target_x = 0.0f;
float target_y = 0.0f;
float xCoords[MAX_COORDS];
float yCoords[MAX_COORDS];
int totalCoords = 0;
int currentTargetIndex = 0;

float angle_error = 0.0f;
float calculated_correction = 0.0f;
float target_distance = 0.0f;

uint32_t last_status_send_time = 0;

int path_set = 0;  // Flag to indicate if a target has been set
int locationReceived = 0;
/* USER CODE END PV */

void SystemClock_Config(void);
/* USER CODE BEGIN PFP */
void HAL_UART_RxCpltCallback(UART_HandleTypeDef *huart);
void execute_command(const char *cmd);
void set_servo_pwm(Servo *servo, uint32_t pulse);
void handle_movement(void);
void handle_rotation(void);
float calculate_angle(float x, float y, float x_next, float y_next);
float distance_to_target(float current_x, float current_y, float target_x,
		float target_y);
float pid_controller(PIDController *pid, float setpoint, float measured_value);
void send_status_to_esp(void);

/* USER CODE END PFP */

/* USER CODE BEGIN 0 */

/**
 * @brief UART Receive Complete Callback.
 * @param huart Pointer to UART handle.
 */
void HAL_UART_RxCpltCallback(UART_HandleTypeDef *huart) {
	if (huart->Instance == USART1) {
		if (UART1_rxBuffer[0] == '\n') { // Assuming commands are newline terminated
			rx_buffer[rx_index] = '\0'; // Null terminate the string
			rx_complete = 1; // Set flag for command complete
			rx_index = 0; // Reset index
		} else {
			rx_buffer[rx_index++] = UART1_rxBuffer[0]; // Store character in buffer
		}
		HAL_UART_Receive_IT(&huart1, UART1_rxBuffer, 1); // Listen for next character
	}
}

/**
 * @brief PID Controller function.
 * @param pid Pointer to PIDController structure.
 * @param setpoint Desired setpoint.
 * @param measured_value Current measured value.
 * @return Control output.
 */
float pid_controller(PIDController *pid, float setpoint, float measured_value) {
	float error = setpoint - measured_value;
	pid->integral += error;

	// Anti-windup: Limit the integral term
	if (pid->integral > pid->integral_limit)
		pid->integral = pid->integral_limit;
	if (pid->integral < -pid->integral_limit)
		pid->integral = -pid->integral_limit;

	float derivative = error - pid->previous_error;
	pid->previous_error = error;

	float output = pid->kp * error + pid->ki * pid->integral
			+ pid->kd * derivative;

	// Limit the output to the maximum correction factor
	if (output > pid->output_limit)
		output = pid->output_limit;
	if (output < -pid->output_limit)
		output = -pid->output_limit;

	return output;
}

/**
 * @brief Handle the rotation of the robot towards the target angle.
 */
void handle_rotation() {
	float target_angle = calculate_angle(current_x, current_y, target_x,
			target_y);
	angle_error = target_angle - current_yaw;

	// Normalize the angle error to always choose the shortest rotation path
	if (angle_error > 180) {
		angle_error -= 360;
	} else if (angle_error < -180) {
		angle_error += 360;
	}

	if (fabsf(angle_error) > ANGLE_THRESHOLD_ROTATE_TO_MOVE) {
		// Normalize the angle error for rotation
		float normalized_angle_error = angle_error / 180.0f;

		// PID-based correction for rotation
		calculated_correction = pid_controller(&rotation_pid, 0.0f,
				normalized_angle_error);

		uint32_t left_right_pwm;

		if (angle_error > 0) {
			// Rotate right: Both motors move forward speed
			left_right_pwm = FORWARD_SLOW + calculated_correction;

			// Ensure PWM values are within valid ranges
			if (left_right_pwm > FORWARD_MAX)
				left_right_pwm = FORWARD_MAX;
			if (left_right_pwm < FORWARD_SLOW)
				left_right_pwm = FORWARD_SLOW;
		} else {
			// Rotate left: Both motors move backward speed
			left_right_pwm = BACKWARD_SLOW - calculated_correction;

			// Ensure PWM values are within valid ranges
			if (left_right_pwm < BACKWARD_MAX)
				left_right_pwm = BACKWARD_MAX;
			if (left_right_pwm > BACKWARD_SLOW)
				left_right_pwm = BACKWARD_SLOW;
		}

		angle_error = 0.0f; // reset angle error for better performance monitoring over udp as only handle_movement angle_error should be captured

		set_servo_pwm(&servo_left, left_right_pwm);
		set_servo_pwm(&servo_right, left_right_pwm);
	} else {
		// Stop rotating and switch to moving state
		set_servo_pwm(&servo_left, SERVO_STOP);
		set_servo_pwm(&servo_right, SERVO_STOP);
		current_state = MOVING;
	}
}

/**
 * @brief Handle the movement of the robot towards the target position.
 */
void handle_movement() {
	target_distance = distance_to_target(current_x, current_y, target_x,
			target_y);
	float target_angle = calculate_angle(current_x, current_y, target_x,
			target_y);
	angle_error = target_angle - current_yaw;

	// Normalize the angle error to [-180, 180]
	if (angle_error > 180.0f) {
		angle_error -= 360.0f;
	} else if (angle_error < -180.0f) {
		angle_error += 360.0f;
	}

	if (target_distance > DISTANCE_THRESHOLD_MOVE_TO_STOP) {
		if (fabsf(angle_error) > ANGLE_THRESHOLD_MOVE_TO_ROTATE) {
			// If the angle error is too large, switch to rotating state
			set_servo_pwm(&servo_left, SERVO_STOP);
			set_servo_pwm(&servo_right, SERVO_STOP);
			current_state = ROTATING;
			return;
		}

		// Normalize the angle error
		float normalized_angle_error = angle_error
				/ ANGLE_THRESHOLD_MOVE_TO_ROTATE;

		// PID-based correction for forward movement
		calculated_correction = pid_controller(&movement_pid, 0.0f,
				normalized_angle_error);

		// Base speeds for both motors
		uint32_t left_pwm = BASE_SPEED_FORWARD;
		uint32_t right_pwm = BASE_SPEED_BACKWARD;

		// Limit the correction to prevent excessive adjustments
		if (calculated_correction > MAX_CORRECTION)
			calculated_correction = MAX_CORRECTION;
		if (calculated_correction < -MAX_CORRECTION)
			calculated_correction = -MAX_CORRECTION;

		// Adjust PWM values based on the correction
		left_pwm += (int32_t) (calculated_correction); // Left motor PWM increases with speed
		right_pwm -= (int32_t) (calculated_correction); // Right motor PWM decreases with speed

		// Ensure PWM values are within valid ranges
		if (left_pwm > FORWARD_MAX)
			left_pwm = FORWARD_MAX;
		if (left_pwm < FORWARD_SLOW)
			left_pwm = FORWARD_SLOW;

		if (right_pwm < BACKWARD_MAX)
			right_pwm = BACKWARD_MAX;
		if (right_pwm > BACKWARD_SLOW)
			right_pwm = BACKWARD_SLOW;

		set_servo_pwm(&servo_left, left_pwm);
		set_servo_pwm(&servo_right, right_pwm);
	} else {
		// Stop the robot when it reaches the target
		set_servo_pwm(&servo_left, SERVO_STOP);
		set_servo_pwm(&servo_right, SERVO_STOP);

		current_state = ROTATING;

		// Hysteresis for distance threshold
		if (target_distance < DISTANCE_THRESHOLD_STOP_TO_MOVE) {
			currentTargetIndex++;
			if (currentTargetIndex < totalCoords) {
				target_x = xCoords[currentTargetIndex];
				target_y = yCoords[currentTargetIndex];
				float target_angle = calculate_angle(current_x, current_y,
						target_x, target_y);
				angle_error = target_angle - current_yaw;
				if (fabsf(angle_error) < ANGLE_THRESHOLD_MOVE_TO_ROTATE) {
					current_state = MOVING;
					return;
				}
			} else {
				current_state = IDLE;
				path_set = 0;
			}
		}
	}
}

/**
 * @brief Calculate the angle between the robot's orientation and the target position.
 * @param x Current x position.
 * @param y Current y position.
 * @param x_next Target x position.
 * @param y_next Target y position.
 * @return Angle in degrees.
 */
float calculate_angle(float x, float y, float x_next, float y_next) {
	// Calculation of the scalar product
	float dot_product = -y * (y_next - y);

	// Length of vectors
	float length_v1 = fabsf(y); // Since v1 is the length of (0, -y), the length corresponds to |y|
	float length_v2 = (float) sqrt(pow(x_next - x, 2) + pow(y_next - y, 2));

	// Calculating the cosine of the angle
	float cos_theta = dot_product / (length_v1 * length_v2);

	// Clamp cos_theta to [-1, 1] to avoid NaNs due to floating point errors
	if (cos_theta > 1.0f)
		cos_theta = 1.0f;
	if (cos_theta < -1.0f)
		cos_theta = -1.0f;

	// Calculation of the angle in radians and conversion to degrees
	float theta_rad = (float) acos(cos_theta);
	float theta_deg = (float) (theta_rad * (180.0 / M_PI));

	// Determining the direction
	if (x_next < x) {
		theta_deg = -theta_deg; // Negative angle if x_next is to the left of x
	}

	return theta_deg;
}

/**
 * @brief Calculate the distance to the target position.
 * @param current_x Current x position.
 * @param current_y Current y position.
 * @param target_x Target x position.
 * @param target_y Target y position.
 * @return Distance to target.
 */
float distance_to_target(float current_x, float current_y, float target_x,
		float target_y) {
	return sqrtf(
			powf(target_x - current_x, 2.0f) + powf(target_y - current_y, 2.0f));
}

/**
 * @brief Execute received command from ESP8266.
 * @param cmd The command string.
 */
void execute_command(const char *cmd) {
	if (strncmp(cmd, "STOP", 4) == 0) {
		set_servo_pwm(&servo_left, SERVO_STOP);
		set_servo_pwm(&servo_right, SERVO_STOP);
		current_state = IDLE;
	} else if (strncmp(cmd, "START_SPINNING", 14) == 0) {
		set_servo_pwm(&servo_left, FORWARD_MAX);
		set_servo_pwm(&servo_right, FORWARD_MAX);
		path_set = 0; 								// Set the path flag
		current_state = SPINNING;
	} else if (strncmp(cmd, "LOCATION_UPDATE", 15) == 0) {
		sscanf(cmd + 16, "%f;%f;%f", &current_x, &current_y, &current_yaw);
		locationReceived = 1;
		if (path_set && current_state == IDLE) {
			target_x = xCoords[currentTargetIndex];
			target_y = yCoords[currentTargetIndex];
			current_state = ROTATING;
		}
	} else if (strncmp(cmd, "PATH_UPDATE", 11) == 0) {
		memset(xCoords, 0, sizeof(xCoords));
		memset(yCoords, 0, sizeof(yCoords));
		totalCoords = 0;
		currentTargetIndex = 0;

		// Extract x and y coordinates and the amount of coordinates
		char x_values[256];  // Buffer for x values
		char y_values[256];  // Buffer for y values
		int amount_of_coordinates = 0;

		// Extract the x values, y values, and the number of coordinates
		sscanf(cmd + 12, "%[^;];%[^;];%d", x_values, y_values,
				&amount_of_coordinates);

		amount_of_coordinates = amount_of_coordinates / 2;

		// Now, x_values contains "x0:x1:x2:...", y_values contains "y0:y1:y2:...", and amount_of_coordinates is an integer
		// Ensure that the number of coordinates does not exceed MAX_COORDS
		totalCoords =
				(amount_of_coordinates > MAX_COORDS) ?
				MAX_COORDS :
														amount_of_coordinates;

		char *token;
		int index = 0;

		// Split x values by ':' and store them in an array
		token = strtok(x_values, ":");
		while (token != NULL && index < totalCoords) {
			xCoords[index++] = atof(token);
			token = strtok(NULL, ":");
		}
		if (index != totalCoords) {
			return;
		}

		// Split y values by ':' and store them in an array
		index = 0;
		token = strtok(y_values, ":");
		while (token != NULL && index < totalCoords) {
			yCoords[index++] = atof(token);
			token = strtok(NULL, ":");
		}
		if (index != totalCoords) {
			return;
		}

		path_set = 1; 				// Set the target flag
		currentTargetIndex = 0;

		if (totalCoords > 0) {
			target_x = xCoords[currentTargetIndex];
			target_y = yCoords[currentTargetIndex];
		}

		current_state = ROTATING;  	// Start with rotating to face the target
	}
}

/**
 * @brief Set the PWM value for a servo motor.
 * @param servo Pointer to the Servo structure.
 * @param pulse PWM value to set.
 */
void set_servo_pwm(Servo *servo, uint32_t pulse) {
	servo->current_pwm = pulse;
	__HAL_TIM_SET_COMPARE(servo->htim, servo->channel, pulse);
}

/**
 * @brief Send the robot's status to ESP8266.
 */
void send_status_to_esp() {
	// Increase buffer size to accommodate arrays
	char status_message[256];

	// Append basic status information
	int len =
			snprintf(status_message, sizeof(status_message),
					"STATE:%d;CURRENT_TARGET_INDEX:%d;MOTOR_L:%lu;MOTOR_R:%lu;ANGLE_ERROR:%.1f;CALCULATED_PID:%.2f;TARGET_DISTANCE:%.2f\n",
					current_state, currentTargetIndex,
					(unsigned long) servo_left.current_pwm,
					(unsigned long) servo_right.current_pwm, angle_error,
					calculated_correction, target_distance);

	// Ensure null-termination
	status_message[sizeof(status_message) - 1] = '\0';

	// Check for truncation
	if (len >= sizeof(status_message)) {
		// Handle the error: truncate, log, etc.
		char error_message[] = "ERROR: Status message truncated.\n";
		HAL_UART_Transmit(&huart1, (uint8_t*) error_message,
				strlen(error_message), HAL_MAX_DELAY);
	}

	// Transmit the status message over UART
	HAL_UART_Transmit(&huart1, (uint8_t*) status_message,
			strlen(status_message), HAL_MAX_DELAY);
}
/* USER CODE END 0 */

/**
 * @brief  The application entry point.
 * @retval int
 */
int main(void) {

	/* MCU Configuration----------------------------------*/

	/* Reset of all peripherals, Initializes the Flash interface and the Systick. */
	HAL_Init();

	/* Configure the system clock */
	SystemClock_Config();

	/* Initialize all configured peripherals */
	MX_GPIO_Init();
	MX_TIM1_Init();
	MX_TIM2_Init();
	MX_USART1_UART_Init();
	MX_I2C1_Init();
	MX_ADC1_Init();
	/* USER CODE BEGIN 2 */

	HAL_GPIO_WritePin(GPIOC, GPIO_PIN_13, GPIO_PIN_SET);
	HAL_Delay(2000);

	/*while (MPU6050_Init(&hi2c1) == 1); //Initialise the MPU6050
	 // calibrate MPU6050
	 for (int interations = 0; interations < CALIB; interations++) {
	 MPU6050_Read_All(&hi2c1, &MPU6050);
	 Gz_mean += MPU6050.Gz;
	 Ax_mean += MPU6050.Ax;
	 Ay_mean += MPU6050.Ay;
	 HAL_Delay(50);
	 }
	 Gz_mean /= CALIB;
	 Ax_mean /= CALIB;
	 Ay_mean /= CALIB;*/

	HAL_TIM_PWM_Init(&htim1);
	HAL_TIM_PWM_Init(&htim2);
	HAL_TIM_PWM_Start(&htim1, TIM_CHANNEL_1);
	HAL_TIM_PWM_Start(&htim2, TIM_CHANNEL_3);
	TIM1->CR1 = 0x01;
	TIM2->CR1 = 0x01;
	HAL_UART_Receive_IT(&huart1, UART1_rxBuffer, sizeof(UART1_rxBuffer)); // interrupt based

	HAL_GPIO_WritePin(GPIOC, GPIO_PIN_13, GPIO_PIN_RESET);
	/* USER CODE END 2 */

	/* Infinite loop */
	/* USER CODE BEGIN WHILE */
	while (1) {
		if (rx_complete) {
			execute_command(rx_buffer); // Process the command
			rx_complete = 0; // Reset the completion flag
		}
		switch (current_state) {
		case ROTATING:
			if (locationReceived) {
				handle_rotation();
				locationReceived = 0;
			}
			break;
		case MOVING:
			if (locationReceived) {
				handle_movement();
				locationReceived = 0;
			}
			break;
		case SPINNING:
			// Spinning is already handled in execute_command
			break;
		case IDLE:
			break;
		default:
		}

		// Send status to ESP8266 every 1000ms
		uint32_t current_time = HAL_GetTick();
		if (current_time - last_status_send_time >= SERIAL_SEND_INTERVAL) {
			last_status_send_time = current_time;
			send_status_to_esp();
		}

		HAL_Delay(10);

		/* USER CODE END WHILE */

		/* USER CODE BEGIN 3 */
	}
	/* USER CODE END 3 */
}

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


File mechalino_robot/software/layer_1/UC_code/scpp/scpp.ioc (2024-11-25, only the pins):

Mcu.UserName=STM32F401CCUx
PA0-WKUP.Signal=ADCx_IN0
PA10.Signal=USART1_RX
PA8.Signal=S_TIM1_CH1
PA9.Signal=USART1_TX
PB0.Signal=GPIO_Output
PB1.Signal=GPIO_Output
PB10.Signal=S_TIM2_CH3
PB3.Signal=GPIO_Output
PB4.Signal=GPIO_Output
PB5.Signal=GPIO_Output
PB8.Signal=I2C1_SCL
PB9.Signal=I2C1_SDA
PC13-ANTI_TAMP.Signal=GPIO_Output
PC14-OSC32_IN.Signal=RCC_OSC32_IN
PC15-OSC32_OUT.Signal=RCC_OSC32_OUT

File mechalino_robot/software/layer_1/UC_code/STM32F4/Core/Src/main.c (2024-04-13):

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
/* Includes ------------------------------------------------------------------*/
#include "main.h"
#include "i2c.h"
#include "tim.h"
#include "usart.h"
#include "gpio.h"

/* USER CODE BEGIN Includes */
#include "mpu6050.h"
//#include <stdio.h>
/* USER CODE END Includes */

/* USER CODE BEGIN PD */
#define STOP 0
#define FORWARD 1
#define BACkWARD 2
#define TURN_RIGHT 3
#define TURN_LEFT 4
#define DIRECT_COMMAND 5
#define SPEED 75

#define COEFF_CORRE 71
#define CALIB_NUNBER 100
#define ACCELERATION 1
/* USER CODE END PD */


/* USER CODE BEGIN PV */
char rx_buffer[20];
char USART_recive = 0;
uint8_t UART1_rxBuffer[2] = { 0 };
uint8_t interrupt10ms = 0;
/* USER CODE END PV */

void SystemClock_Config(void);
/* USER CODE BEGIN PFP */
MPU6050_t MPU6050;
/* USER CODE END PFP */

/* USER CODE BEGIN 0 */
void HAL_UART_RxCpltCallback(UART_HandleTypeDef *huart) //go inside each time a character is send on serial
{
	static uint8_t length = 0;
	HAL_UART_Receive_IT(&huart1, UART1_rxBuffer, 1);
	if (!(((UART1_rxBuffer[0] == '\n') || (UART1_rxBuffer[0] == '\r'))
			&& (length == 0))) //if recive real data ( not just "\r\n")
	{
		rx_buffer[length] = UART1_rxBuffer[0]; //copy the recived caractere on buffer
		length++;
		if ((UART1_rxBuffer[0] == '\n') || (UART1_rxBuffer[0] == '\r')
				|| (length == 20)) //if end of sending data, quit
				{
			if (length > 1)
				USART_recive = 1; //message is complete recived
			length = 0;
		}
	}
}
void motor(int16_t MotL, int16_t MotR) //PWM mcontrole (1 ms -> backward / 1.5 ms -> no moove / 2 ms -> forward)
{
	uint32_t cntL, cntR;
	MotL = MotL + 100; //put an offset (0 to 200)
	MotR = MotR + 100; //put an offset (0 to 200)
	cntL = ((MotL * 2000) / 200) + 2000; //value of PWM start at 2000 and finish at 4000
	cntR = ((MotR * 2000) / 200) + 2000; //value of PWM start at 2000 and finish at 4000
	TIM1->CCR1 = cntL; //put value on TIMERs registers
	TIM2->CCR3 = cntR; //put value on TIMERs registers
}
/* USER CODE END 0 */

/**
 * @brief  The application entry point.
 * @retval int
 */
int main(void) {
	/* MCU Configuration-------------------------------*/

	/* Reset of all peripherals, Initialises the Flash interface and the Systick. */
	HAL_Init();

	/* USER CODE BEGIN Init */
	uint8_t action = 0;
	char ReciveOrder = ' ';
	double angle, distance, derived;
	int16_t Argument = 0;
	int16_t Argument2 = 0;
	int16_t delay;
	/* USER CODE END Init */

	/* Configure the system clock */
	SystemClock_Config();

	/* Initialize all configured peripherals */
	MX_GPIO_Init();
	MX_I2C1_Init();
	MX_TIM1_Init();
	MX_TIM2_Init();
	MX_USART1_UART_Init();
	/* USER CODE BEGIN 2 */

	HAL_Delay(100);

	while (MPU6050_Init(&hi2c1) == 1)
		; //Init Accelerometer

	//Gpio (IR)
	GPIOB->MODER |= (0x02 << GPIO_MODER_MODER0_Pos); //B0 in output
	GPIOB->MODER |= (0x02 << GPIO_MODER_MODER1_Pos); //B1 in output
	GPIOB->MODER |= (0x02 << GPIO_MODER_MODER3_Pos); //B3 in output
	GPIOB->MODER |= (0x02 << GPIO_MODER_MODER4_Pos); //B4 in output
	GPIOB->MODER |= (0x02 << GPIO_MODER_MODER5_Pos); //B5 in output

	GPIOB->OSPEEDR |= (0x03 << GPIO_OSPEEDR_OSPEED0_Pos); //B0 in  Very high speed
	GPIOB->OSPEEDR |= (0x03 << GPIO_OSPEEDR_OSPEED1_Pos); //B1 in  Very high speed
	GPIOB->OSPEEDR |= (0x03 << GPIO_OSPEEDR_OSPEED3_Pos); //B3 in  Very high speed
	GPIOB->OSPEEDR |= (0x03 << GPIO_OSPEEDR_OSPEED4_Pos); //B4 in  Very high speed
	GPIOB->OSPEEDR |= (0x03 << GPIO_OSPEEDR_OSPEED5_Pos); //B5 in  Very high speed

	GPIOB->ODR &= ~(GPIO_ODR_OD0 | GPIO_ODR_OD1 | GPIO_ODR_OD3 | GPIO_ODR_OD4
			| GPIO_ODR_OD5); //Put the pins B0,1,3,4,5 to 0

	HAL_UART_Receive_IT(&huart1, UART1_rxBuffer, 1);

	//init timer 1 (PWM) Left servo
	HAL_TIM_PWM_Init(&htim1);
	HAL_TIM_PWM_Start(&htim1, TIM_CHANNEL_1);
	TIM1->CCMR1 = 0x60; //Configure in PWM mode
	TIM1->PSC = 41; //(41+1)divide 84MHz/42 = 2MHz
	TIM1->ARR = 40000; //PWM duty cycle -> 2MHz/40 000 = 50Hz
	TIM1->CCR1 = 3000; //put PWM at 1.5ms (1/2 000 000)*3000 = 1.5ms state do nothing
	TIM1->CR1 = 0x01; // Turn on PWM

	//init timer 2 (PWM) Right servo
	HAL_TIM_PWM_Init(&htim2);
	HAL_TIM_PWM_Start(&htim2, TIM_CHANNEL_3);
	TIM2->CCMR2 = 0x60; //Configure in PWM mode
	TIM2->PSC = 41; //(41+1)divide 84MHz/42 = 2MHz
	TIM2->ARR = 40000; //PWM duty cycle -> 2MHz/40 000 = 50Hz
	TIM2->CCR3 = 3000; //put PWM at 1.5ms (1/2 000 000)*3000 = 1.5ms state do nothing
	TIM2->CR1 = 0x01; // Turn on PWM

	//init timer 11 (10ms) sampling accelerometer
	RCC->APB2ENR |= RCC_APB2ENR_TIM11EN; //Enable timer 11 clock
	TIM11->CR1 |= TIM_CR1_OPM; //set timer on counter mode
	TIM11->DIER |= TIM_DIER_UIE; //Enable interrupt of timer 11
	TIM11->PSC = 83; //div by 83+1
	TIM11->ARR = 10000; //1000*10ms -> 10ms

	NVIC_EnableIRQ(TIM1_TRG_COM_TIM11_IRQn); //enable unterrupt

	//init timer 10 (10ms) sampling accelerometer             /////////////////To be completed
	RCC->APB2ENR |= RCC_APB2ENR_TIM10EN; //Enable timer 10 clock
	TIM10->CR1 |= TIM_CR1_OPM; //set timer on counter mode
	TIM10->DIER |= TIM_DIER_UIE; //Enable interrupt of timer 10
	TIM10->PSC = 6; //div by 6+1
	TIM10->ARR = 150; // 12.5us -> 80 KHz
	NVIC_EnableIRQ(TIM1_UP_TIM10_IRQn); //enable unterrupt     ////////////////////
	//TIM10->CR1 |= TIM_CR1_CEN;//Start sampling ADC

	//ADC Configurqtion
	//ADC1_0 pin A0
	GPIOA->MODER |= (0x03 << GPIO_MODER_MODE0_Pos);
	RCC->APB2ENR |= RCC_APB2ENR_ADC1EN;	//Enqble ADC clock source
	ADC1->CR1 |= ADC_CR1_EOCIE;	//Enable End Of Convertion interrupt
	ADC1->CR1 |= ADC_CR1_DISCEN;	//Enable discontinuous mode
	ADC1->CR2 |= ADC_CR2_ADON;	//Enable ADC
	ADC1->SMPR2 = 0x02;
	//ADC1->CR2 |= ADC_CR2_SWSTART;//stqrt convertion
	//while((ADC1->SR & ADC_SR_EOC) == ADC_SR_EOC);//wait the end of convertion

	HAL_Delay(50);	//wait ESP8266 starting
	char data[200];
	int N = 50;
	double sm = 0.0;
	double mean = 0.0;
	double offset = 0.0;
	int8_t turnvalue = 0, calib, accel, decel;
	int i;
	/* USER CODE END 2 */

	/* Infinite loop */
	/* USER CODE BEGIN WHILE */
	while (1) {
		/////////////////////////// start
		if (USART_recive == 1)	//if complete message is recived
		{
			Argument = 0;
			ReciveOrder = rx_buffer[0];	//the command
			if (ReciveOrder == 'C'){
				char temp,temp2;
				sscanf(&rx_buffer, "%c%hd%c%hd", &temp, &Argument, &temp2, &Argument2);
				temp = 'd';
			}
			else
				sscanf(&rx_buffer[1], "%d", &Argument);	//first param
//		  Argument -= 10;
			USART_recive = 0;
			HAL_GPIO_TogglePin(GPIOC, GPIO_PIN_13);	//toggle debug pin
		}

		switch (ReciveOrder) {
			case '0': {
				action = STOP;
				break;
			}
			case 'F': {
				action = FORWARD;
				break;
			}
			case 'B': {
				action = BACkWARD;
				break;
			}
			case 'R': {
				action = TURN_RIGHT;
				break;
			}
			case 'L': {
				action = TURN_LEFT;
				break;
			}
			case 'C': {
				action = DIRECT_COMMAND;
				break;
			}
		}
		switch (action) {
			case STOP: {
				motor(0, 0);	//motor do nothing
				break;
			}
			case FORWARD: {
				angle = 0;
				TIM11->CR1 |= TIM_CR1_CEN;
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

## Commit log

2023-08-14 overhead camera is connected
2023-08-15 old repository integration
    [Assembly.scad, Head.scad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]
2023-08-16 fixed transfrom from camera to table added
2023-08-16 static transform frames order corrected
2023-08-18 folder's name corrected
    [Assembly.scad, Head.scad, body.stl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]
2023-08-18 wheel conector modified
    [Assembly.scad, wheels1.3mf, wheels1.scad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]
2023-08-18 wheel connector modified
    [wheels1.3mf, wheels1.scad]
2023-08-22 wheel connector corrected
    [wheels1.3mf, wheels1.scad, wheels1.stl]
2023-08-22 PID Controller improved
2023-08-22 PID Controller updated
2023-08-22 stm32 code updated to be more accurate
2023-08-25 stm32f4 code switched to command mode
2023-08-25 camera calibration
2023-08-25 camera calibration improved
2023-09-09 new robot head
    [Head.scad]
2023-09-17 stm code unkown problems are fixed
    [main.c]
2024-02-19 new obstacle holder
    [obstacle_holder.3mf, obstacle_holder.scad, obstacle_holder.stl]
2024-02-20 using cv2 for camera
2024-02-27 Revert "using cv2 for camera"
    This reverts commit 24741410c78f922b2bdb0db2638b53c9410f1446.
2024-02-28 Update camera transform and error calculation in corners_publisher.py
2024-03-19 udp camera client added
2024-03-19 udp camera server
2024-04-13 Serial connection and MPU6050 works
    [scpp Debug.cfg]
2024-04-15 WIP new head for robot | PID WIP
    [Head.3mf, Head.scad, Head.stl]
2024-04-17 WIP rotation (+offset error) + movement
    [core.ino, main.c]
2024-05-21 3D designs compatible with layer 2
    [layer2.scad]
2024-05-24 WIP LNF
    [layer2.3mf, layer2.scad, layer2.stl]
2024-06-18 Added detailed comments and documentation to camera_server.py
2024-06-29 Added redesigned schematic and simulation of second layer
    [Mechalino_Second_Layer.PrjPcb, Mechalino_Second_Layer.SchDoc, Mechalino_Second_Layer_v2.SchDoc]
2024-07-06 Created PCB and finished routing.
    [Mechalino_Second_Layer.PcbDoc, Mechalino_Second_Layer.PrjPcb, Mechalino_Second_Layer.SchDoc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]
2024-07-09 Updated to fit internship student
    [Mechalino_Second_Layer.GBL, Mechalino_Second_Layer.GBO, Mechalino_Second_Layer.GBP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]
2024-07-11 updated pcb layout
    [Mechalino_Second_Layer.GBL, Mechalino_Second_Layer.GBO, Mechalino_Second_Layer.GBP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]
2024-08-16 Implemented goto xy and registration logic with ROS
    [Mechalino_Second_Layer.GBL, Mechalino_Second_Layer.GBO, Mechalino_Second_Layer.GKO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]
2024-09-30 Movement improved via PID
2024-10-06 fixed esp8266 code to send serial correct again
    [TCPConnection.ino, main.c, scpp.ioc]
2024-10-10 PID control improvement plus udp visualization tool for Robots and Table
2024-11-25 Updated second layer
    [Mechalino_Second_Layer.PcbDoc]

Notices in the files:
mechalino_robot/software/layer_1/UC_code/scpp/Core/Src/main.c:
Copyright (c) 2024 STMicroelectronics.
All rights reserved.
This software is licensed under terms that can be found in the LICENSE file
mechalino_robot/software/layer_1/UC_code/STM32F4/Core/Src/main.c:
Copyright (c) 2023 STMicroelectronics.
